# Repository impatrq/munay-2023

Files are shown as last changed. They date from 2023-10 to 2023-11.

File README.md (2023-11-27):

<div align="center">

# [Proyecto Munay - IMPA TRQ](https://www.instagram.com/proyecto_munay/)

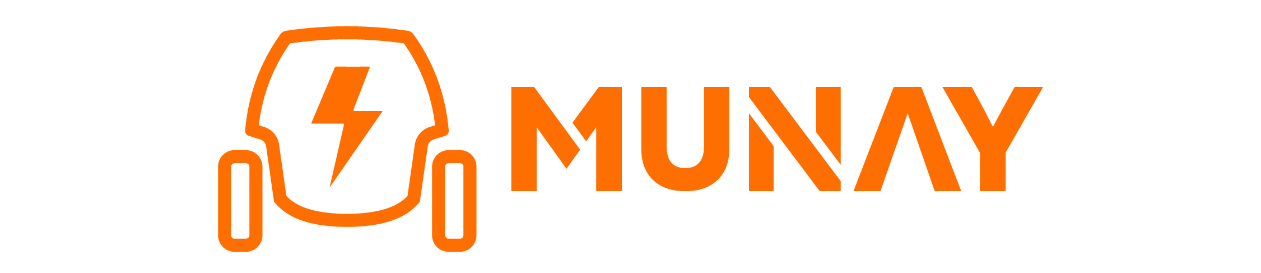
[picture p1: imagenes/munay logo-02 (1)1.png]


&nbsp;

| Página web | Email | Instagram |
|---|---|---|
|[Munay Web](https://proyectomunay.github.io/)|munay.impatrq@gmail.com|[@proyecto_munay](https://www.instagram.com/proyecto_munay/)|

&nbsp;

</div>

## ¿Qué es Munay?
Es un vehículo eléctrico diseñado específicamente para recorrer las pistas de las plazas aeroportuarias y llevar a cabo tareas como controlar la presencia de aves, señalero en pista y supervisar su estado general. Con este proyecto, buscamos acercar las últimas tecnologías al ámbito aeroportuario para modernizar sus procesos de control, supervisión y seguridad.

## ¿De dónde surgió la idea?
El proyecto Munay surgió a partir de una visita al aeropuerto Jorge Newbery (aeroparque), en la que se observó las diferentes modalidades de trabajo utilizadas y una de éstas fue la recorrida de pista. Se identificó que esta tarea conlleva mucho tiempo y recursos, y se consideró que era necesario buscar una solución innovadora para mejorar la eficiencia y la sostenibilidad en la industria aeroportuaria. Esto contribuiría a reducir los costos de operación y mantenimiento que se necesitan para un vehículo a combustión interna, que son los que se usan actualmente en este ámbito.

## Nuestra solución
Munay se destaca como un sistema de supervisión simplificado y altamente eficiente para la detección de FOD. Un vehículo eléctrico especialmente adaptado con cuatro cámaras estratégicamente ubicadas. Estas cámaras no solo proporcionan una vista precisa de la superficie terrestre, sino que, gracias a algoritmos de inteligencia artificial, también pueden detectar FOD tanto en tierra como en el cielo. Desarrollaremos un software personalizado que es esencial para esta solución. Cuando se conecta a Munay, ofrece una interfaz de usuario intuitiva que muestra las imágenes en tiempo real de las cuatro cámaras. La simplicidad es clave, los operadores solo necesitan traer su propia computadora de trabajo y conectarla al vehículo a través de USB en el soporte personalizado del auto.

## ¿Quiénes somos?

Somos un grupo de alumnos de E.E.S.T. N°7 "Taller Regional Quilmes" (IMPA).

### Basile, Ignacio Javier
* 📷 Instagram: basilee05

* 📧 ignaciojavierbasile@gmail.com

* LinkedIn: https://www.linkedin.com/in/demian-heis/

### Echezuria Gonzalez, Jorge Luis
* 📷 Instagram: jorgeechezuria_

* 📧 jlechezuria@gmail.com

* LinkedIn: https://www.linkedin.com/in/jorge-echezuria-60962a245/

### Heis, Demian Hernán
* 📷 Instagram: demian.h_

* 📧 demiheis@gmail.com

* LinkedIn: https://www.linkedin.com/in/demian-heis/

### Minaya Palomino, Jesús Eduardo
* 📷 Instagram: jesusminaya_

* 📧 jesusminayapalomino@gmail.com

* LinkedIn: http://www.linkedin.com/in/jesus-minaya-53a314292

### Ordoñez, Lucero Soledad Rubi
* 📷 Instagram: lucero092_

* 📧 lucerosoledad56@gmail.com
  
* LinkedIn: https://www.linkedin.com/in/lucero-soledad-rub%C3%AD-ordo%C3%B1ez-6a7ab429b/

### Retamar, Faustina

* 📷 Instagram: faustinaar_

* 📧 retamarfaustinaa@gmail.com

* LinkedIn: https://www.linkedin.com/in/faustina-retamar-43ab861a6/

### Rios, Celeste Aylen
* 📷 Instagram: celestearios

* 📧 celesteaylenrios@gmail.com

* LinkedIn: https://www.linkedin.com/in/celestearios/

<div align="center">

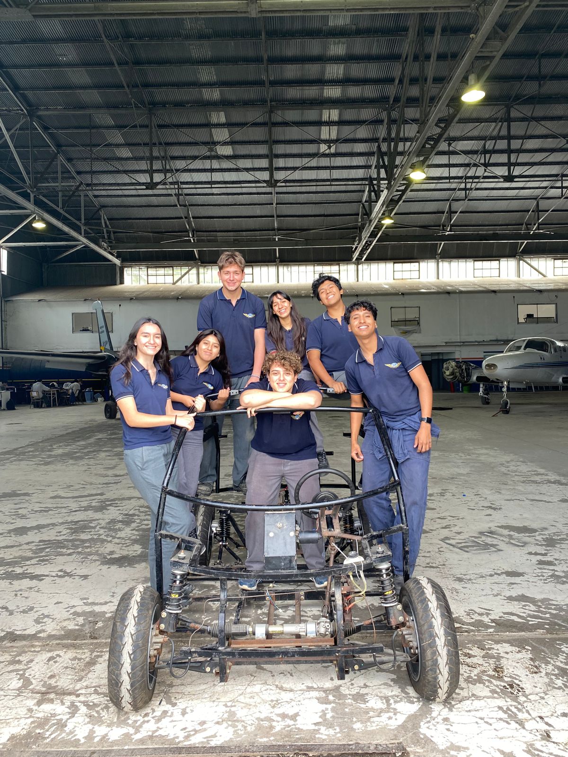
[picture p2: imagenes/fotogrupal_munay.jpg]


</div>

## ¿Cómo contactarnos?

* 📧 Email: munay.impatrq@gmail.com

* 🌐 Página Web: https://proyectomunay.github.io/

* 📷 Instagram: @proyecto_munay

* 🗞️ Linktr.ee: https://linktr.ee/proyecto_munay

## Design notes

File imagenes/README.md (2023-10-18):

<div align="center">

# [Proyecto Munay - IMPA TRQ](https://www.instagram.com/proyecto_munay/)



&nbsp;

| Página web | Email | Instagram |
|---|---|---|
|[Munay Web](https://www.google.com.ar/?hl=es)|munay.impatrq@gmail.com|[@proyecto_munay](https://www.instagram.com/proyecto_munay/)|

&nbsp;

</div>

## ¿Qué es Munay?

## ¿De dónde surgió la idea?

## ¿Cómo funciona?

## Tecnologías utilizadas

### Aplicación móvil

- Ionic con React
- Typescript
- Bootstrap

### Interfaz gráfica

- Electron
- React
- Typescript
- Bootstrap

### Esquemáticos

- KiCad

### Página web

- Next.js
- Typescript
- TailwindCSS
- Bootstrap

### Base de datos

- Firebase Realtime Database

### Microcontrolador

- uPython

### Planos

- AutoCAD

## ¿Quiénes somos?

Somos un grupo de alumnos de E.E.S.T. N°7 "Taller Regional Quilmes" (IMPA).

### Basile, Ignacio Javier
--> 📷 Instagram: basilee05

--> 📧 ignaciojavierbasile@gmail.com

### Echezuria Gonzalez, Jorge Luis
--> 📷 Instagram: jorgeechezuria_

--> 📧 jlechezuria@gmail.com

### Heis, Demian Hernán
--> 📷 Instagram: demian.h_

--> 📧 @gmail.com

### Minaya, Jesús Eduardo
--> 📷 Instagram: jesusminaya_

--> 📧 @gmail.com

### Ordoñez, Lucero Soledad Rubi
--> 📷 Instagram: lucero092_

--> 📧 @gnmail.com

### Retamar, Faustina
--> 📷 Instagram: faustinaar_

--> 📧 @gmail.com

### Rios, Celeste Aylen
--> 📷 Instagram: celestearios

--> 📧 @gmail.com

<div align="center">



</div>

## ¿Cómo contactarnos?

* 📧 Email: munay.impatrq@gmail.com

* 🌐 Página Web: xx

* 📷 Instagram: @proyecto_munay

* 🗞️ Linktr.ee: https://linktr.ee/proyecto_munay

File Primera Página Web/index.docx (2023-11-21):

Munay - IMPA TRQ

- Home
- About
- Contact

Auto eléctrico

para una supervisión eficiente

¿Qué es y cuál es el objetivo?

Munay es un vehículo eléctrico que será utilizado para la recorrida de pista en las plazas aeroportuarias, cumpliendo tareas como el control de aves, señalero de pista, y haciendo una supervisión general del estado de la misma.

Con MUNAY acercaremos las nuevas tecnologías en el ámbito aeroportuario. Modernizando sus procesos de control, supervisión y seguridad.

En base a las ventajas de utilizar MUNAY como vehículo de control destaca...

La referida a la reducción de emisiones de gases de efecto invernadero y de otros contaminantes en el aire.

Los costos de operación son más bajos en comparación con los vehículos de combustión interna, los que generalmente son utilizados en este ámbito, así resultaría esto en un ahorro significativo para el aeropuerto a largo plazo.

Visita a aeroparque

En febrero de 2023 hicimos una visita al aeropuerto "Jorge Newbery" (aeroparque) e investigando un poco nos dimos cuenta que es una zona con mucha energía solar sin aprovecharse, debido a ello crearemos un sistema de carga solar para el vehículo y así reducir el costo y mantenimiento que necesita un auto a combustión interna (que son los utilizados en la actualidad).

Instagram: @proyecto_munay | Linktree: @proyecto_munay | Mail: munay.impatrq@gmail.com

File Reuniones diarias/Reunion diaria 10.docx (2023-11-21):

# Miembros:

- BASILE, Ignacio Javier
- ECHEZURIA GONZALEZ, Jorge Luis
- HEIS, Demian Hernan
- MINAYA PALOMINO, Jesús Eduardo
- ORDOÑEZ, Lucero Soledad Rubí
- RETAMAR, Faustina
- RIOS, Celeste Aylen

# Trabajo actual

Planificación de las actividades a trabajar con OM001 ; OM003 ; HU001 ; HU002 ; HU009

# Expectativa del día

1. Terminaciones de la GUI
a. HU002G4 (https://trello.com/c/hfgtvepv) -> Minaya Jesús

2. Soldar

a. OM001B3 (https://trello.com/c/YOWDd1Iy) -> Echezuria Jorge; Heis Demian

3. Definir la frecuencia del envío

a. HU001E2 (https://trello.com/c/4T0kK5Ga) -> Retamar Faustina

4. Conexión y Prueba del Circuito

a. OM003C2 (https://trello.com/c/Cb8Cf4MF) -> Basile Ignacio, Ordoñez Lucero

5. Interfaz gráfica

a. HU009C3 (https://trello.com/c/GDZwJFuE) -> Ordoñez Lucero, Rios Celeste

# Observación:

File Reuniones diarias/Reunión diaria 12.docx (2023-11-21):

# Miembros:

- BASILE, Ignacio Javier
- ECHEZURIA GONZALEZ, Jorge Luis
- HEIS, Demian Hernan
- MINAYA PALOMINO, Jesús Eduardo
- ORDOÑEZ, Lucero Soledad Rubí
- RETAMAR, Faustina
- RIOS, Celeste Aylen

# Trabajo actual

Planificación de las actividades a trabajar con OM004 ; HU002 ; OM003 ; HU018

# Expectativa del día

1. Crear el programa que entrene la IA
a. HU002C2 (https://trello.com/c/GfMNkTXK) -> Minaya Jesús

2. Diseño de piezas

a. OM004A1 (https://trello.com/c/0t3vdllK) -> Basile Ignacio; Heis Demian

3. Carpeta de campo

a. HU018A (https://trello.com/c/BrOlQ3Z9) -> Echezuria Jorge ; Minaya Jesús

4. Calcular costos de pantalla y Terminaciones de la GUI

a. HU002F2 (https://trello.com/c/AScfl0pu) y HU002G4 (https://trello.com/c/hfgtvepv) -> Retamar Faustina; Rios Celeste

5. Terminaciones de la GUI

a. HU002G4 (https://trello.com/c/hfgtvepv) -> Retamar Faustina ; Rios Celeste

6. Reconexión de la palanca de cambios

a. OM003B6 (https://trello.com/c/YXXsG0NT) -> Echezuria Jorge; Ordoñez Lucero

# Observación:

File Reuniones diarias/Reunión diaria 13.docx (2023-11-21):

# Miembros:

- BASILE, Ignacio Javier
- ECHEZURIA GONZALEZ, Jorge Luis
- HEIS, Demian Hernan
- MINAYA PALOMINO, Jesús Eduardo
- ORDOÑEZ, Lucero Soledad Rubí
- RETAMAR, Faustina
- RIOS, Celeste Aylen

# Trabajo actual

Planificación de las actividades a trabajar con HU002 ; HU009 ; OM003; OM004; OM001

# Expectativa del día

1. Calcular costos de pantalla
a. HU002F2 (https://trello.com/c/AScfl0pu) -> Retamar Faustina

2. Botonera de la interfaz gráfica

a. HU002G6 (https://trello.com/c/lPkaCEpE) -> Retamar Faustina

3. Investigación de la comunicación-interfaz

a. HU009B2 (https://trello.com/c/D3MURqXc) -> Ordoñez Lucero; Rios Celeste

4. Diseño de piezas

a. OM004A1 (https://trello.com/c/0t3vdllK) -> Basile Ignacio ; Heis Demian

5. Switch (llave)

a. OM003B6 (https://trello.com/c/q51soJW4) -> Ordoñez Lucero

6. Pintar y lijar estructura

a. OM003D1 (https://trello.com/c/RGVBPgmT) -> Echezuria Jorge; Rios Celeste

7. Crear el programa que entrene la IA

a. HU002C2 (https://trello.com/c/GfMNkTXK) -> Minaya Jesús

8. Corrección de torsión en la parrilla

a. OM001C (https://trello.com/c/eUWS69it) -> Heis Demian

# Observación:

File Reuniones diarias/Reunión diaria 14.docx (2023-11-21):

# Miembros:

- BASILE, Ignacio Javier
- ECHEZURIA GONZALEZ, Jorge Luis
- HEIS, Demian Hernan
- MINAYA PALOMINO, Jesús Eduardo
- ORDOÑEZ, Lucero Soledad Rubí
- RETAMAR, Faustina
- RIOS, Celeste Aylen

# Trabajo actual

Planificación de las actividades a trabajar con HU002 ; HU009 ; OM004; OM001

# Expectativa del día

1. Botonera de la interfaz gráfica

a. HU002G6 (https://trello.com/c/lPkaCEpE) -> Retamar Faustina

2. Investigación de la comunicación-interfaz

a. HU009B2 (https://trello.com/c/D3MURqXc) -> Ordoñez Lucero; Rios Celeste

3. Diseño de piezas

a. OM004A1 (https://trello.com/c/0t3vdllK) -> Basile Ignacio

4. Inferencia utilizando Opencv

a. HU002D2 (https://trello.com/c/JhfQWf2p) -> Minaya Jesús

5. Corrección de torsión en la parrilla

a. OM001C (https://trello.com/c/eUWS69it) -> Echezuria Jorge ; Heis Demian

# Observación:

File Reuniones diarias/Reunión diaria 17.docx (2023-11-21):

# Miembros:

- BASILE, Ignacio Javier
- ECHEZURIA GONZALEZ, Jorge Luis
- HEIS, Demian Hernan
- MINAYA PALOMINO, Jesús Eduardo
- ORDOÑEZ, Lucero Soledad Rubí
- RETAMAR, Faustina
- RIOS, Celeste Aylen

# Trabajo actual

Planificación de las actividades a trabajar con HU009; HU002; OM003; OM004

# Expectativa del día

1. Transmisión de datos

a. HU009B4 (https://trello.com/c/2LAP4XD2) -> Rios Celeste; Echezuria Jorge

2. Pruebas de la botoneras en la interfaz

a. HU002G7 (https://trello.com/c/7uwNMmGb) -> Retamar Faustina; Minaya Jesús

3. Conexión de alimentación tablet/monitor

a. OM003B6 (https://trello.com/c/DJl1E43K) -> Ordoñez Lucero

4. ]Instalación

a. OM004B3 (https://trello.com/c/c1TSl2E6) -> Basile Ignacio; Heis Demian

# Observación:

- Retamar Faustina (llegó tarde)
- Heis Demian (llegó tarde)

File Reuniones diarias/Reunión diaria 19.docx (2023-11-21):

# Miembros:

- BASILE, Ignacio Javier
- ECHEZURIA GONZALEZ, Jorge Luis
- HEIS, Demian Hernan
- MINAYA PALOMINO, Jesús Eduardo
- ORDOÑEZ, Lucero Soledad Rubí
- RETAMAR, Faustina
- RIOS, Celeste Aylen

# Trabajo actual

Planificación de las actividades a trabajar con HU002; HU009; OM004

# Expectativa del día

1. Transmisión de los datos

a. HU009B4 (https://trello.com/c/2LAP4XD2) -> Echezuria Jorge ; Rios Celeste

2. Fabricación de piezas

a. OM004A2 (https://trello.com/c/7y6zeGLg) -> Basile Ignacio ; Heis Demian

3. Pruebas de las botoneras en la interfaz

a. HU002G7 (https://trello.com/c/7uwNMmGb) -> Minaya Jesús

4. Diseñar y probar prompt para las alertas

a. HU002E4 (https://trello.com/c/ufm9qXok) -> Retamar Faustina

Observación:

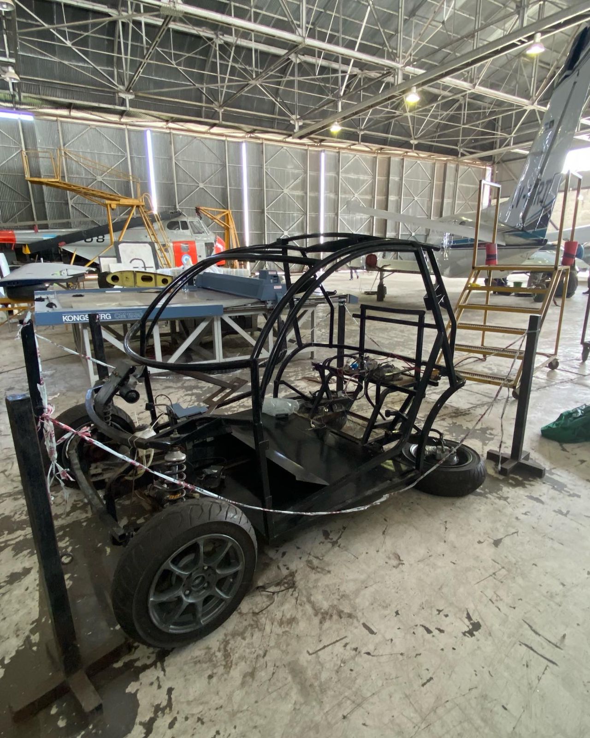
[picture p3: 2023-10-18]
Munay Web/images/gallery-images/gallery-image-7.jpg

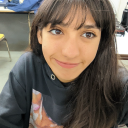
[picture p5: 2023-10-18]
Munay Web/images/user-images/rios.png

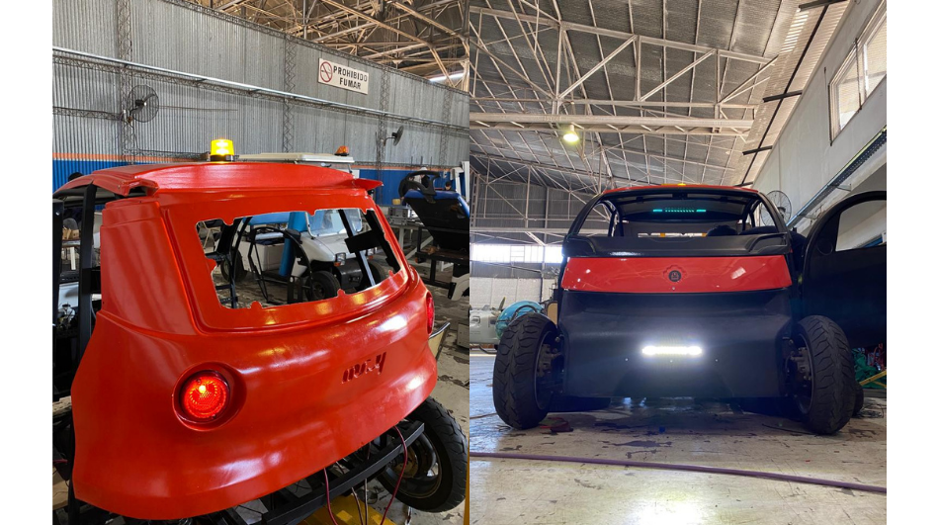
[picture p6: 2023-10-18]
Munay Web/images/gallery-images/gallery-image-16.png

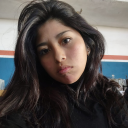
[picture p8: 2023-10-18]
Munay Web/images/user-images/ordoñez.png

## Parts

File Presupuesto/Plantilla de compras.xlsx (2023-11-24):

Adquirido | Cantidad | Componente | Link de referencia | Mejor precio | Por cantidad | Compra? | Proveedor | Prestado? | Escuela? | Devolver a:
FALSE | 1 | Ejemplo Sensor Presion Diferencial Mpx5100dp | CLICK (https://articulo.mercadolibre.com.ar/MLA-923254064-sensor-presion-diferencial-mpx5100dp-_JM) | $0.00 | $0.00 | FALSE | Intor (https://www.intor.com.ar/) | FALSE | FALSE
TRUE | 2 | Baterías | CLICK | $4000.00 | $8000.00 | FALSE | Aerocommander | TRUE | TRUE | Aerocommander
TRUE | 2 | Cable Usb a RS232 | CLICK (https://articulo.mercadolibre.com.ar/MLA-611815713-cable-adaptador-usb-a-serial-rs232-xtatil-local-belgrano-_JM) | $7.44 | $14.88 | TRUE | xTATIL (https://www.xtatil.com.ar/) | FALSE | FALSE
TRUE | 1 | MAX232 | CLICK (https://articulo.mercadolibre.com.ar/MLA-739213410-max-232-max-232-max232-max232cpe-rs-232-ttl-transceiver-_JM) | $3.25 | $3.25 | TRUE | Cyberofice (https://www.cyberofice.com.ar/) | FALSE | FALSE
TRUE | 1 | Conector DB9 Hembra | CLICK (https://articulo.mercadolibre.com.ar/MLA-800022729-adaptador-usb-20-a-hembra-db9-serie-hembra-_JM) | $1.20 | $1.20 | TRUE | AndesPC (https://www.andespc.com/) | FALSE | FALSE
TRUE | 2 | Tablet de 5" 2 GB de RAM Android | CLICK | $0.00 | $0.00 | FALSE | ENACOM (https://www.enacom.gob.ar/) | TRUE | FALSE | ENACOM
TRUE | 2 | Faros Led 160x80 - 120W | CLICK (https://articulo.mercadolibre.com.ar/MLA-867482995-par-de-faros-barras-auxiliar-led-cree-120w-spotflood-a-vip-_JM) | $32.34 | $64.68 | TRUE | Encedido Oeste | FALSE | FALSE
TRUE | 1 | Microcontrolador BeagleBone Black | CLICK (https://articulo.mercadolibre.com.ar/MLA-748742044-beaglebone-black-4g-arm-cortex-a-8-1ghz-4gb-original-rev-c-_JM) | $130.56 | $130.56 | FALSE | Fabrizio Carlassara | TRUE | FALSE | Carlassara Fabrizio
TRUE | 3 | Webcam Usb Xiaomi Imilab | CLICK (https://articulo.mercadolibre.com.ar/MLA-902320072-webcam-camara-web-para-pc-full-hd-1080p-con-microfono-noga-e-_JM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) | $9.14 | $27.42 | FALSE | ELECTROPOINT (https://www.electropoint.com.ar/) | FALSE | FALSE
TRUE | 1 | Cámara Watec modelo wat-01u2 | CLICK | $0.00 | $0.00 | FALSE | Diego Palmieri | TRUE | FALSE | Palmieri Diego
TRUE | 1 | micro-HDMI a HDMI | CLICK (https://articulo.mercadolibre.com.ar/MLA-901428738-cable-premium-micro-hdmi-a-hdmi-1-metro-hd-1080p-3d-vention-_JM) | $10.63 | $10.63 | TRUE | REDNETCorp (https://rednetcorp.com.ar/) | FALSE | FALSE
TRUE | 3 | Cables 5m Rojo-5m Verde-5m Marrón | CLICK (https://articulo.mercadolibre.com.ar/MLA-741624441-cable-unipolar-15-mm-negro-nomalizado-x-100m-fonseca-e631-_JM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) | $0.22 | $3.37 | TRUE | Eléctrica 361 (https://www.e631.com.ar/) | FALSE | FALSE
TRUE | 1 | Adaptador USB a HDMI Dehuka | CLICK (https://www.mercadolibre.com.ar/adaptador-compatible-macbook-pro-adaptador-usb-a-hdmi-video-1080p-dehuka/p/MLA21079140) | $10.17 | $10.17 | TRUE | DEHUKA (https://www.dehuka.com/) | FALSE | FALSE
TRUE | 2 | Amortiguador Trasero Jorsa | CLICK (https://articulo.mercadolibre.com.ar/MLA-1116735145-amortiguadores-vastago-corto-tras-peugeot-106-91-jorsa-_JM) | $114.00 | $228.00 | FALSE | Jorsa (http://www.jorsa.com.ar/index.htm) | FALSE | TRUE
TRUE | 2 | Motores QS motors | CLICK (https://www.qsmotor.com/product/3000w-205-car-motor/) | $310.00 | $620.00 | FALSE | QS Motors (https://www.qsmotor.com/) | FALSE | TRUE
TRUE | 1 | Parilla Delantera genérica | CLICK (https://articulo.mercadolibre.com.ar/MLA-871916024-juego-2-parrillas-de-suspension-c-rotula-renault-clio-12-_JM) | $142.00 | $142.00 | FALSE | RODINAG (https://www.rodinag.com/) | FALSE | TRUE
TRUE | 1 | Amortiguador Delantero Jorsa | CLICK (https://articulo.mercadolibre.com.ar/MLA-1116735145-amortiguadores-vastago-corto-tras-peugeot-106-91-jorsa-_JM) | $114.00 | $114.00 | FALSE | Jorsa (http://www.jorsa.com.ar/index.htm) | FALSE | TRUE
TRUE | 1 | Estructura Angulo Cuadrado genérico 22m | CLICK | $52.00 | $52.00 | FALSE | - | FALSE | TRUE
TRUE | 2 | Controladores Kelly KLS6022H | CLICK (https://kellycontroller.com/shop/brushless/) | $65.00 | $130.00 | FALSE | Kelly (https://kellycontroller.com/) | FALSE | TRUE
TRUE | 1 | Modulo Gps Gy-neo6mv2 Con Antena Raspberry Pic | CLICK (https://articulo.mercadolibre.com.ar/MLA-681823978-modulo-gps-gy-neo6mv2-con-antena-raspberry-pic-avr-arduino-_JM) | $8.00 | $8.00 | TRUE | DUAITEK | FALSE | FALSE
TRUE | 1 | Raspberry pi 4 | CLICK (https://articulo.mercadolibre.com.ar/MLA-885844516-raspberry-pi-4-model-b-4gb-ram-usb-c-element-14-_JM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) | $110.00 | $110.00 | FALSE | Sergio Medina | TRUE | FALSE | Medina Sergio
FALSE | 1 | - | CLICK | $0.00 | $0.00 | FALSE |  | FALSE | FALSE
FALSE | 1 | - | CLICK | $0.00 | $0.00 | FALSE |  | FALSE | FALSE
FALSE | 1 | - | CLICK | $0.00 | $0.00 | FALSE |  | FALSE | FALSE
FALSE | 1 | - | CLICK | $0.00 | $0.00 | FALSE |  | FALSE | FALSE
FALSE | 1 | - | CLICK | $0.00 | $0.00 | FALSE |  | FALSE | FALSE
FALSE | 1 | - | CLICK | $0.00 | $0.00 | FALSE |  | FALSE | FALSE
FALSE | 1 | - | CLICK | $0.00 | $0.00 | FALSE |  | FALSE | FALSE
FALSE | 1 | - | CLICK | $0.00 | $0.00 | FALSE |  | FALSE | FALSE

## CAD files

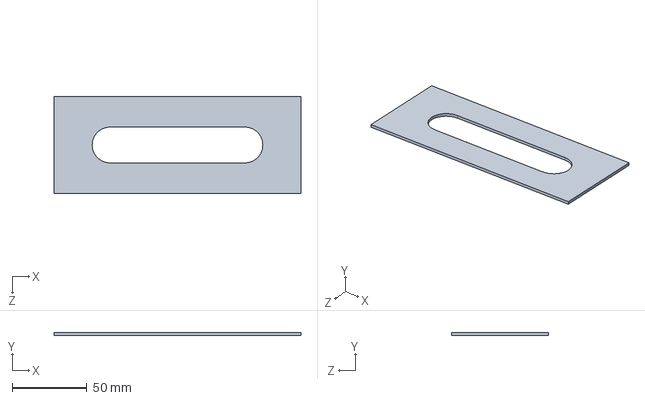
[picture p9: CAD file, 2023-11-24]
Diseños 3D/Archivos Solid Works/Base para Acelerador.SLDPRT
165.0 x 2.00 x 65.0 mm

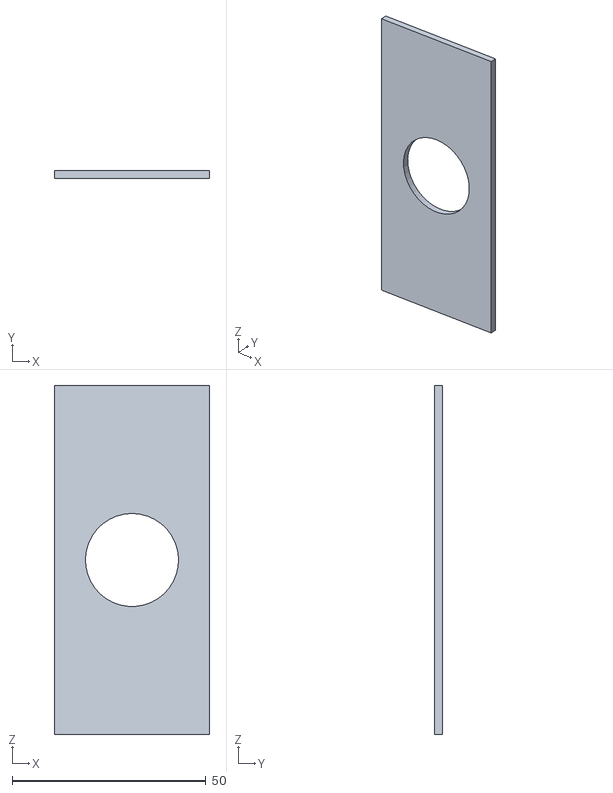
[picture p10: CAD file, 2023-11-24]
Diseños 3D/Archivos STL/Base para Acelerador.STL
40.0 x 2.00 x 90.0

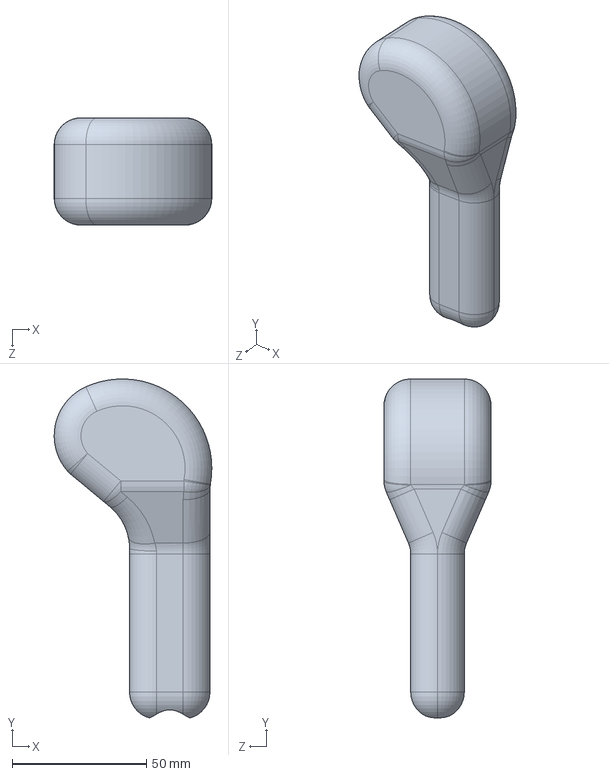
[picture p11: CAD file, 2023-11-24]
Diseños 3D/Archivos Solid Works/Palanca de Cambios.SLDPRT
58.8 x 126.4 x 40.0 mm

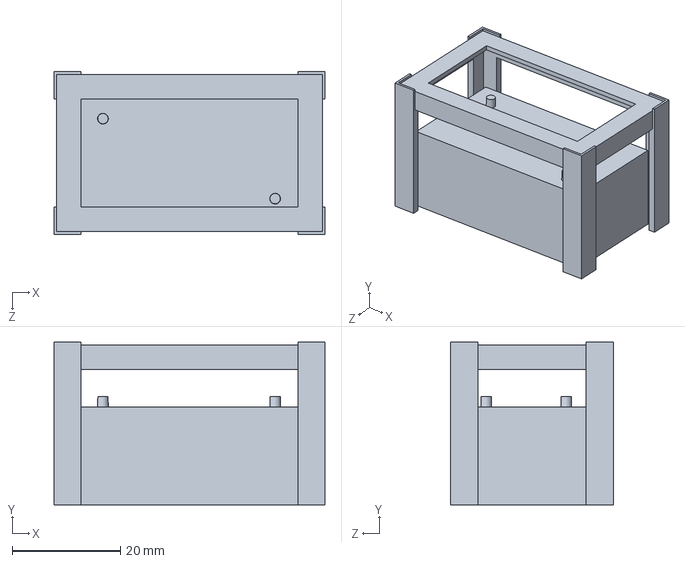
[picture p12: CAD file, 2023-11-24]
Diseños 3D/Archivos Solid Works/Estrructura Caja.SLDPRT
50.0 x 30.0 x 30.0 mm

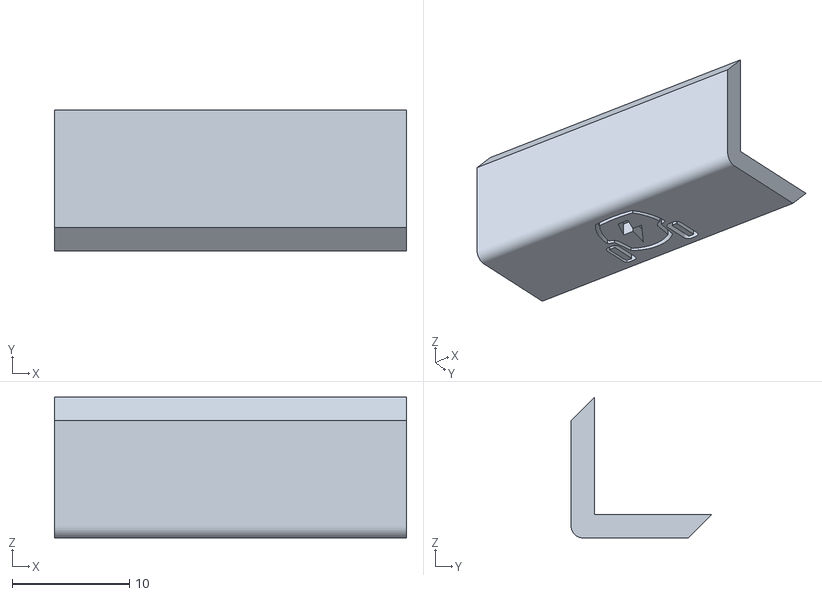
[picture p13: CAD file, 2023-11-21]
Diseños 3D/Archivos STL/Sold Arriba Embellesedor.STL
30.0 x 12.0 x 12.0

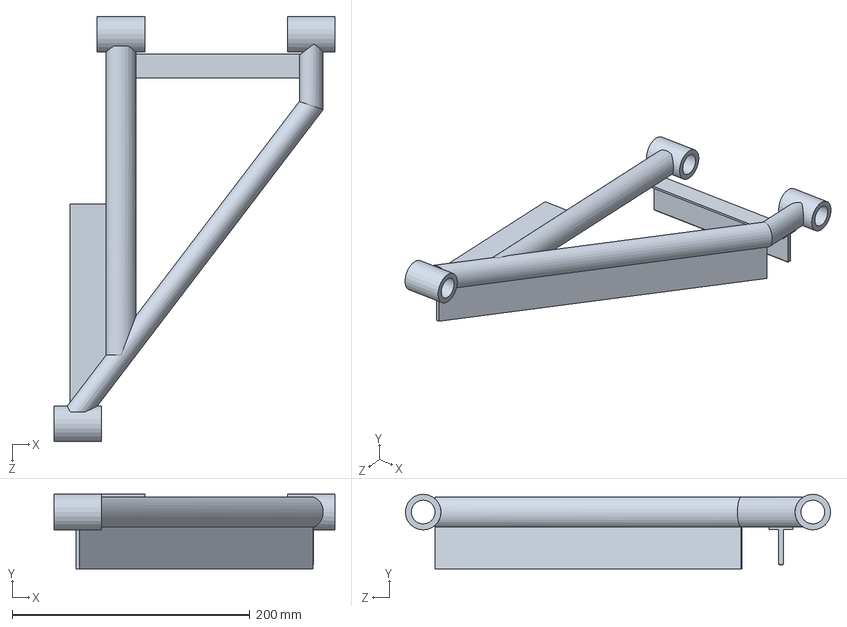
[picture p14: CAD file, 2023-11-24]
Diseños 3D/Archivos Solid Works/Parrilla Reforzada.SLDPRT
236.4 x 62.7 x 357.7 mm

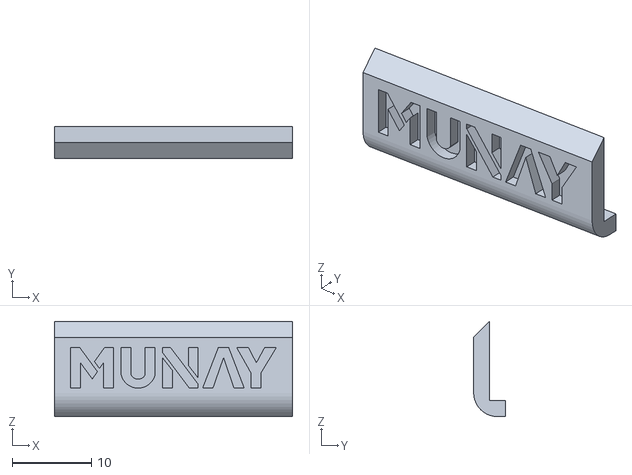
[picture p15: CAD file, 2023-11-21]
Diseños 3D/Archivos STL/Sold Abajo Embellesedor.STL
30.0 x 4.00 x 12.0

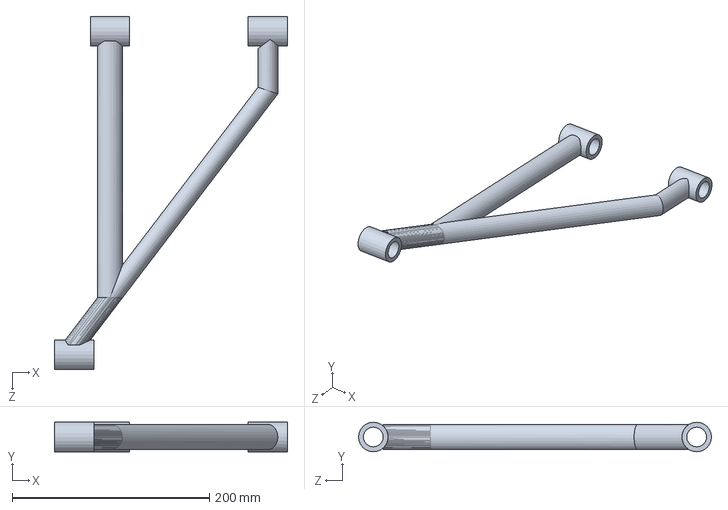
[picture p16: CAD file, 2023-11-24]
Diseños 3D/Archivos Solid Works/Parrilla Sin Refuerzo.SLDPRT
236.4 x 30.0 x 357.7 mm

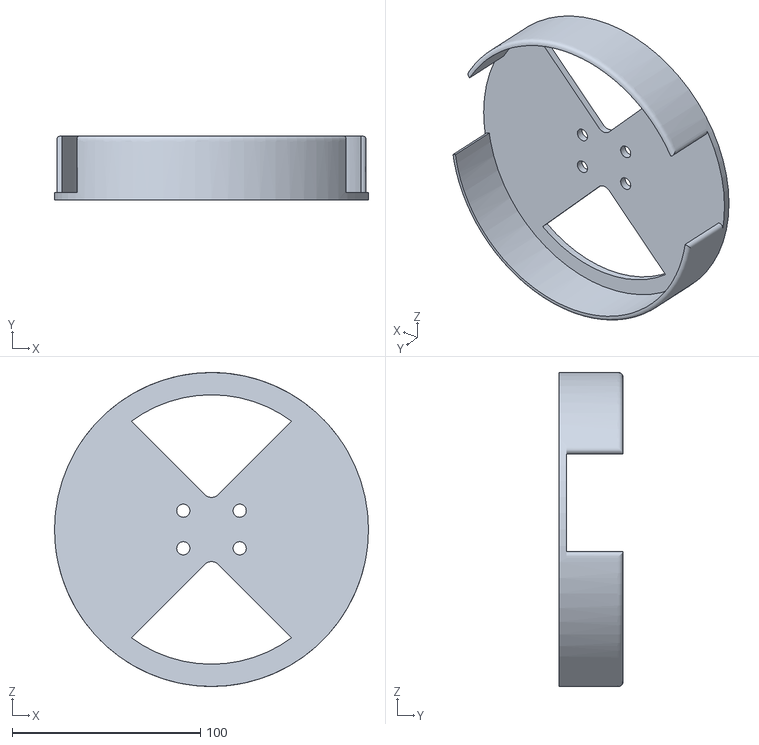
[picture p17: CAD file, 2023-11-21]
Diseños 3D/Archivos STL/Cubierta Volante.STL
167.0 x 34.0 x 167.0

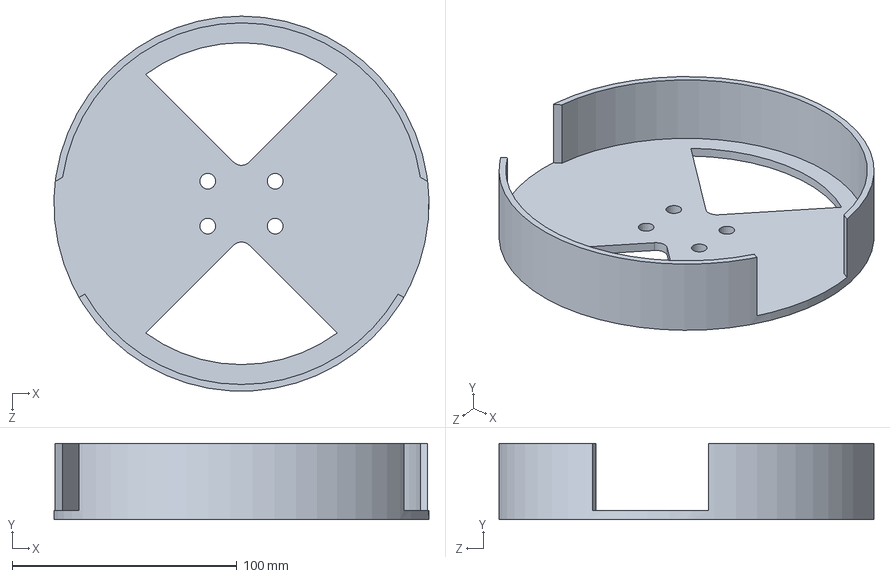
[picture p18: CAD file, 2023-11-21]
Diseños 3D/Archivos Solid Works/Soporte volante.SLDPRT
167.0 x 34.0 x 166.9 mm

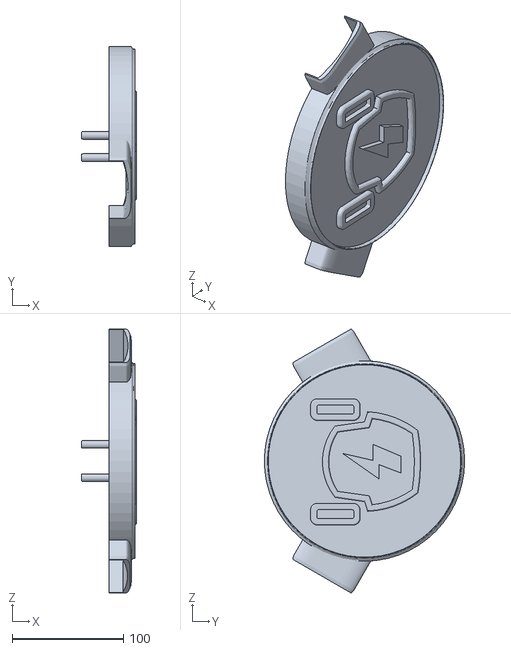
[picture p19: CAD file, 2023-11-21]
Diseños 3D/Archivos STL/Soporte de Volante.STL
49.0 x 180.0 x 237.2

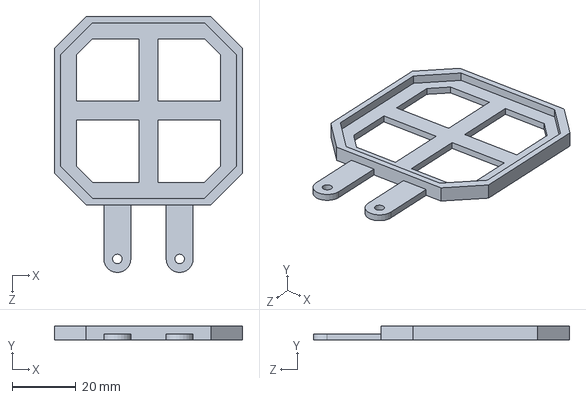
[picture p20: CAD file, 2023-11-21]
Diseños 3D/Archivos Solid Works/Soporte usb.SLDPRT
59.1 x 4.50 x 80.3 mm

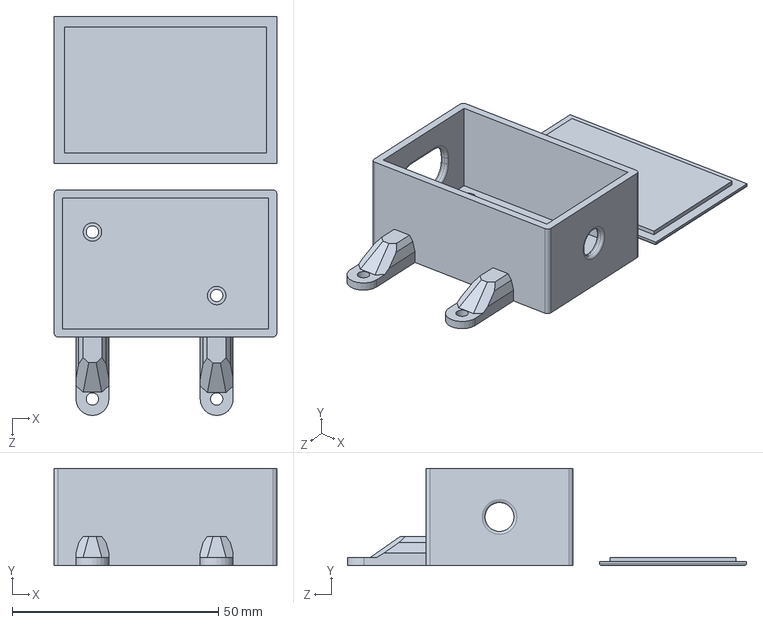
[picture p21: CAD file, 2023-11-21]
Diseños 3D/Archivos Solid Works/Reg Para Tablet Jack.SLDPRT
54.0 x 23.5 x 96.7 mm

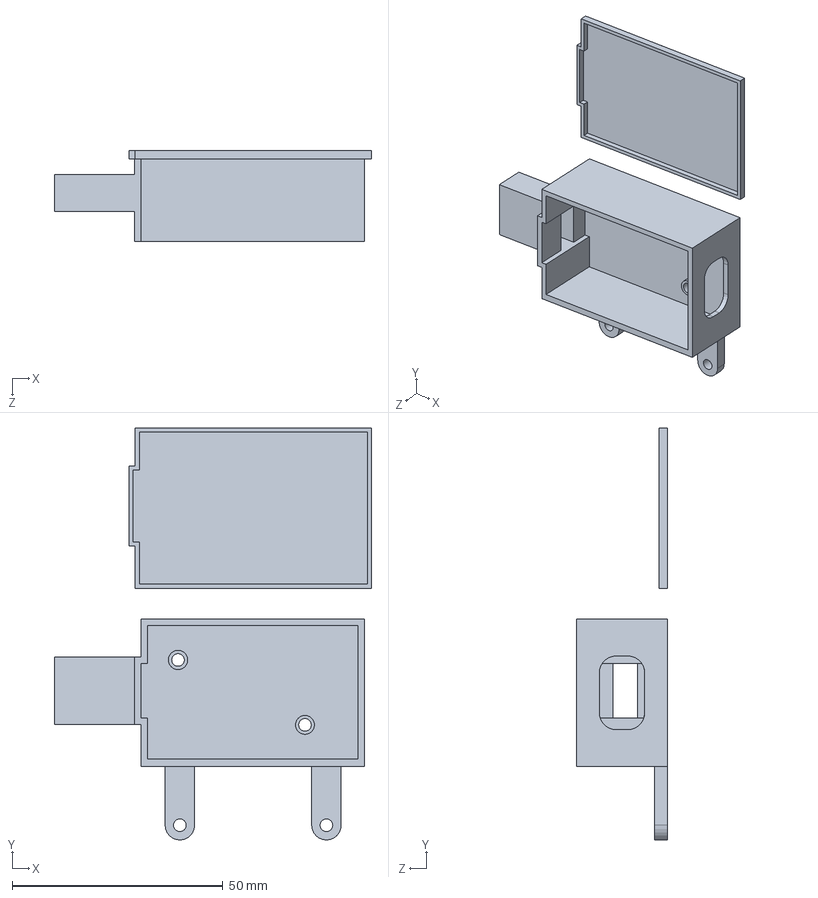
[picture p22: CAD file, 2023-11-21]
Diseños 3D/Archivos Solid Works/Reg Para Tablet A.SLDPRT
75.2 x 97.7 x 21.5 mm

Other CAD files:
Diseños 3D/Archivos STL/STL Palanca.STL
Diseños 3D/Archivos STL/Soporte usb.STL
Diseños 3D/Archivos STL/Reg Para Tablet Jack.STL
Diseños 3D/Archivos STL/Reg Para Tablet A.STL
Diseños 3D/Archivos STL/Camara Frente.STL
Diseños 3D/Archivos STL/Camara Piso.STL
Diseños 3D/Archivos STL/Covertor de rueda+Logo.STL
Diseños 3D/Archivos STL/Embellesedor Parte DER.STL
Diseños 3D/Archivos STL/Embellesedor Parte IZQ.STL
Diseños 3D/Archivos STL/Funda Tablet Bien 3.STL
Diseños 3D/Archivos STL/Logo Frente del auto.STL
Diseños 3D/Archivos Solid Works/Camara Frente.SLDPRT
Diseños 3D/Archivos Solid Works/Camara Piso.SLDPRT
Diseños 3D/Archivos Solid Works/Covertor de rueda+Logo.SLDPRT
Diseños 3D/Archivos Solid Works/Cubierta Volante.SLDPRT
Diseños 3D/Archivos Solid Works/Embellesedor Parte DER.SLDPRT
Diseños 3D/Archivos Solid Works/Embellesedor Parte IZQ.SLDPRT
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

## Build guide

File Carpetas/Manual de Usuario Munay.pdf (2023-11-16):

# MUNAY

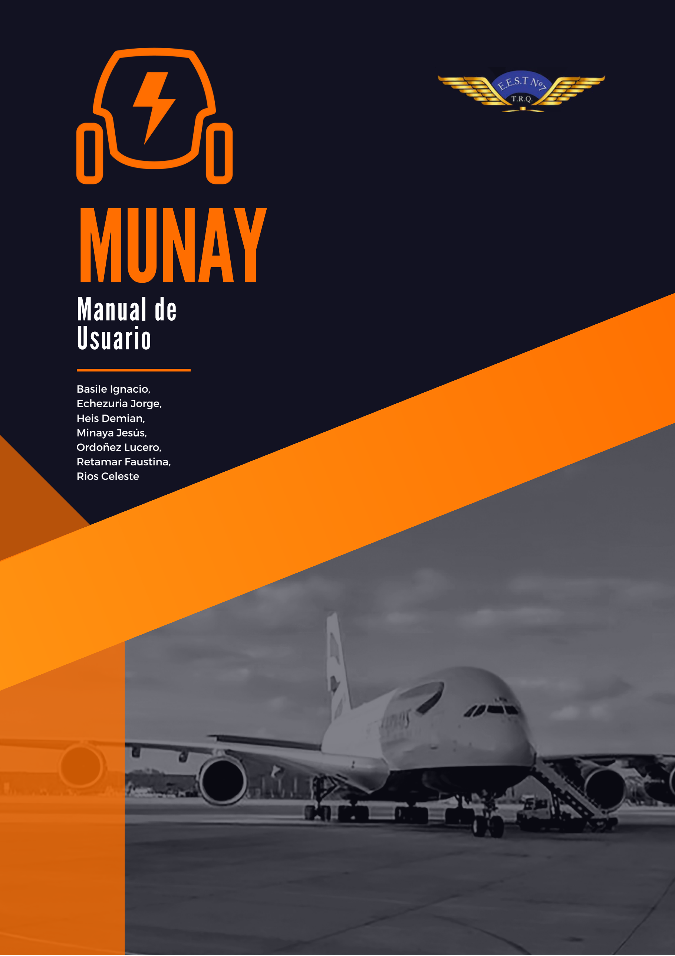
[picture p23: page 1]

# Manual de Usuario

Basile Ignacio, Echezuria Jorge, Heis Demian, Minaya Jesús, Ordoñez Lucero, Retamar Faustina, Rios Celeste

# ÍNDICE

1. Introducción | 3
2. Seguridad para conducir | 3
3. Baterías | 4
3.1 Baterías traseras | 4
3.1.1 Procedimiento de carga | 4
3.1.2 Precauciones, atenciones y advertencias | 6
4. Autonomía | 8
4.1 Recomendaciones para mantener su autonomía | 8
5. Sistemas de propulsión y electrónica | 8
5.1 Motores | 8
5.2 Controladores | 8
6. Componentes del sistema | 9
6.1 Cámaras | 9
6.2 Inteligencia Artificial | 10
6.3 Interfaz gráfica | 10
6.3.1 Pasos para iniciar la interfaz gráfica | 11
6.4 Visualización de imágenes en tiempo real | 12
6.5 Botones y configuración de la interfaz grafica | 13
6.6 Bot de Telegram | 16
6.6.1 Configuración del destinatario | 16
6.6.1.1 Obtener su ID de chat en Telegram | 17
6.7 Detectar FOD | 17
6.7.1 Procedimientos luego de detección de FOD | 17
7. Luces | 18

### 7.1 Ubicación de las luces 7.2 Precauciones

## Guía para el Personal de Mantenimientos de Aeropuertos

Antes de encender tu vehículo, asegúrate de que el conector de carga esté desconectado.
Antes de encender tu vehículo, asegúrate de que la perilla de cambio de marcha esté en posición de neutro (N).
Enciende tu vehículo y comprueba el dashboard, la interfaz gráfica, todas las luces de señalización, y las cámaras. Asegúrate de que las cámaras estén limpias y sin obstrucciones que puedan afectar la detección de FOD.
Para asegurarte de no obstruir los pedales, verificá que no haya obstáculos de en el área de los mismos.
Comprueba que el sistema de iluminación y la sirena funcione correctamente
Para garantizar que viajes de manera segura, revisa los asientos y cinturones de seguridad
Antes de conducir, asegúrate de abrochar apropiadamente el cinturon de seguridad, revisar el ángulo del retrovisor, y fijarte que las puertas estén completamente cerradas.
Comprueba el porcentaje de carga de la batería en el tablero de instrumentos.

# 1. INTRODUCCIÓN

En el mundo dinámico de la aviación, la seguridad es primordial. Enfrentando el desafío de los "restos de objetos extraños" (FOD), Munay redefine la vigilancia en las pistas aeroportuarias. Desde diminutas piezas metálicas hasta objetos más imponentes, asegurando que cada rincón del aeropuerto esté libre de obstáculos, garantizando así la seguridad y eficiencia en la operación aeroportuaria.

# 2. SEGURIDAD PARA CONDUCIR

¡Antes de operar el vehiculo asegurese de haber leído atentamente el manual de usuario!

Apague el vehículo antes de cargar las batería. Es necesario que el vehículo se encuentre apagado para mayor seguridad. Tanto para las dos baterias traseras verifique que las especificaciones de ambas se ajusten a Munay y que estén en buen estado, sin daños, fugas o signos de desgaste.
Para la conexiones de carga asegúrese que el cargador de las baterías esté en buenas condiciones

# 3. BATERIAS

Cómo cargar las baterías
Cargar las baterías de Munay es una tarea esencial para garantizar su funcionamiento seguro y confiable. A continuación, se proporciona una guía paso a paso que explica cómo cargar estas baterías, teniendo en cuenta que esto puede variar según el tipo de aeronave del que se haya extraído su batería.

Para ello, utiizaremos un cargador, en donde se va a enchufar en el lado izquierdo del vehículo, con una ficha de tipo industrial . Este estará conectado directamente a las baterías aeronáuticas.

## 3.1 Baterías traseras

Estas baterías son fundamentales para Munay, ya que, estas alimentan al Controlador Kelly que es una pieza clave para el arranque del vehículo.

### 3.1.1 Procedimiento de carga

Antes de comenzar el proceso de carga de las baterías aeronáuticas en Munay, asegúrate de seguir estos pasos de preparación:

Asegúrese que las conexiones del cable de carga estén firmes y seguras. Si no está bien ajustada, puede ocasionar una carga fantasma en las baterías, o deformarlas. Configure el equipo de carga de acuerdo a las especificaciones del fabricante y las necesidades de las baterías aeronáuticas:
Ajuste el voltaje y la corriente de carga según las especificaciones de las baterías. No exceda los límites recomendados.
Establezca el tiempo de carga de acuerdo a las necesidades de las baterías y su nivel de descarga.
Encienda el cargador de baterías de acuerdo con las instrucciones del fabricante.
Durante el proceso de carga, supervise continuamente el estado de las baterías y el equipo de carga para detectar cualquier anomalía. Recuerde evitar el aumento de temperatura en las baterías.
Cuando se haya completado el proceso de carga desconecte el cargador de baterías del cable de carga y apáguelo.

No excedas los límites de carga recomendados para evitar daños a las baterías y posibles riesgo.
No permitas que los cables de carga entren en contacto con objetos metálicos que puedan causar cortocircuitos.
Nunca intentes cargar baterías dañadas o con fugas. Sustitúyelas antes de la carga.
La carga de baterías del vehículo es una tarea crítica que debe realizarse con precaución y siguiendo las pautas del fabricante. Si no está seguro de cómo hacerlo, consulte a un profesional de mantenimiento de aeronaves calificado.

## 3.1.2 Precauciones, Atenciones y Advertencias

# 4. AUTONOMIA

Debe de tener en cuenta que su tiempo máximo de uso está estimado en una hora, en la que usted recorrerá un aproximadamente una distancia de 30Km. Además el vehículo consume 0,0216 kilovatios - hora por kilometro que recorre.

## 4.1 Recomendaciones para mantener su autonomía

Procure conducir a velocidades reducidas para proteccion de la autonomía. Evite aceleraciones y frenadas bruscas que provocarían aumentar el consumo de energía.

# 5. SISTEMA DE PROPULSION Y ELECTRONICA

## 5.1 Motores

El nombre del motor es QSWP 48V 2000W1 70612. El modelo de ambos motores es QS de ejes unicos, ideales para coches electricos. Su voltaje nominal es de 48v . La potencia nominal es de 2000 vatios, lo que significa que esta es la potencia máxima que el motor puede suministrar continuamente en condiciones normales.

## 5.2 Controladores

El vehículo cuenta con los controladores Kelly KLS6022H. Los controladores de motor programables Kelly brindan controles eficientes, suaves y silenciosos para motocicletas eléctricas, carritos de golf y go-karts, así como control de motores industriales.

Cámara Frontal: Ubicada en la parte delantera del vehículo.Detecta problemas en la pista, como desgaste o acumulación de objetos extraños (F.O.D.).
Cámaras Superiores (tres): Situadas en la parte superior del vehículo con un ángulo de separación de 120 grados. Amplían significativamente el campo de visión sin necesidad de salir del vehículo. Y detectan el movimiento de aves, lo que contribuye a prevenir riesgos para la seguridad aeroportuaria.

# 6. COMPONENTES DEL SISTEMA

Los componentes del sistema se refieren al conjunto de elementos que conforman la llamativa tecnología de Munay, y estos son las cámaras, la inteligencia artificial con su interfaz grafica, el dashboard, etc. A continuación se explican y detallan cada una de ellas para su correcta operacion.

## 6.1 Cámaras

Munay integra un conjunto de cámaras de alto rendimiento, cada una con funciones específicas.

1.

2. (https://e-vehicle.eu/KellyKLS-HUserManualV1.10.pdf)

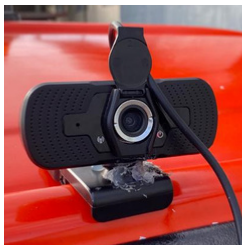
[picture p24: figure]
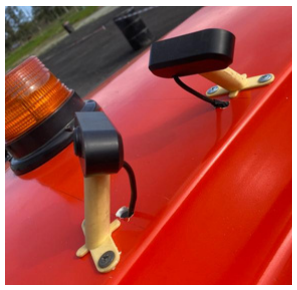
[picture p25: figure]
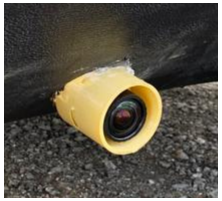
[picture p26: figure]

## 6.2 Inteligencia Artificial

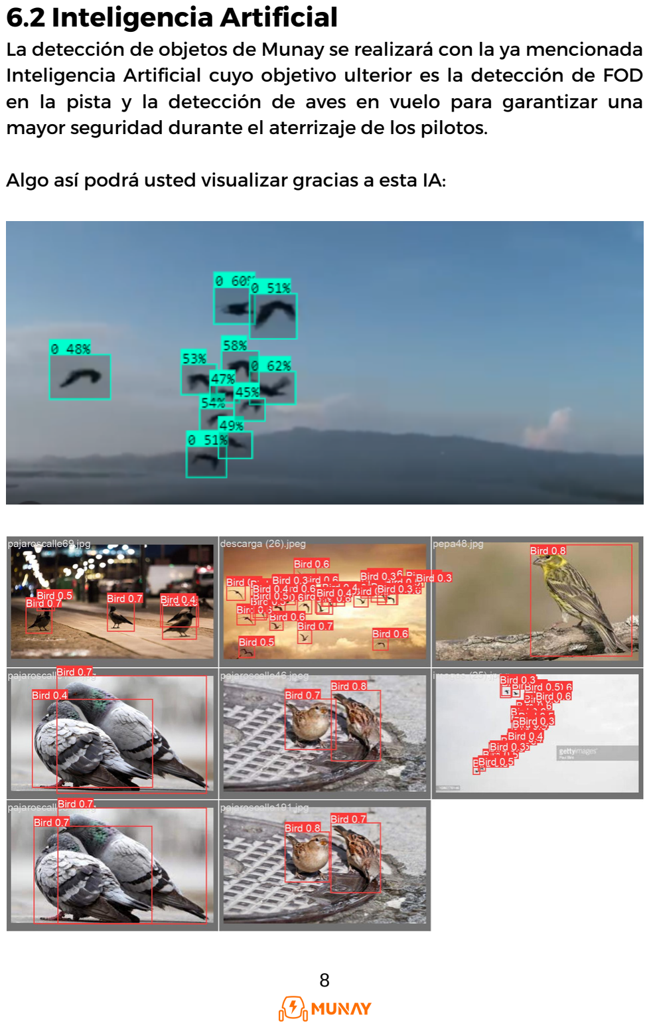
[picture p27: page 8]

La detección de objetos de Munay se realizará con la ya mencionada Inteligencia Artificial cuyo objetivo ulterior es la detección de FOD en la pista y la detección de aves en vuelo para garantizar una mayor seguridad durante el aterrizaje de los pilotos.

Algo así podrá usted visualizar gracias a esta IA: (https://e-vehicle.eu/KellyKLS-HUserManualV1.10.pdf)

El instalador de la interfaz gráfica se encuentra en la página web de Munay. Puede acceder a ella mediante el siguiente link o QR.

## 6.3 Interfaz Gráfica

Para utilizar la inteligencia artificial, se empleará una interfaz gráfica a través de la cual se podrá activar la IA. Esta interfaz estará disponible para su descarga desde la página oficial de Munay.

6.3.1 Pasos para descargar tu Interfaz gráfica (https://e-vehicle.eu/KellyKLS-HUserManualV1.10.pdf)

https://proyectomunay.github.io/

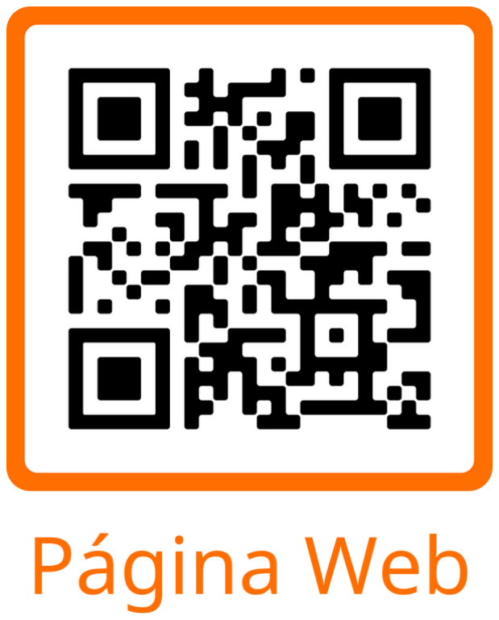
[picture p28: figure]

Seleccione el ícono que se presenta en la foto. Al apretarlo, se le descargará automáticamente el instalador de la interfaz gráfica y, ese mismo aparecerá en la barra de descargas de su plataforma.

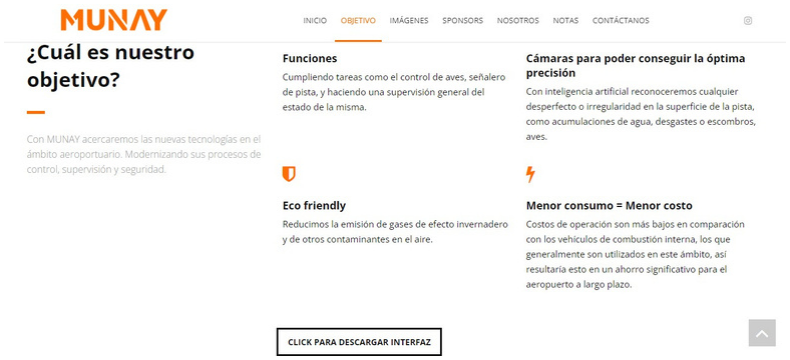
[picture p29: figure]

Luego que se haya cargado el instalador, se procede a ejecutar el programa. Le aparecerá una ventana de “selección de idioma que va a tener la interfaz gráfica”.

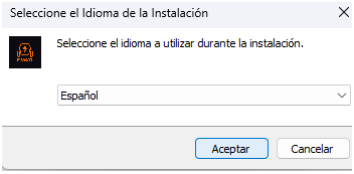
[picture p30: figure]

Después, le aparecerá una ventana de “escribir la contraseña del instalador del programa”. Esta contraseña se la daremos cuando compre nuestro servicio.

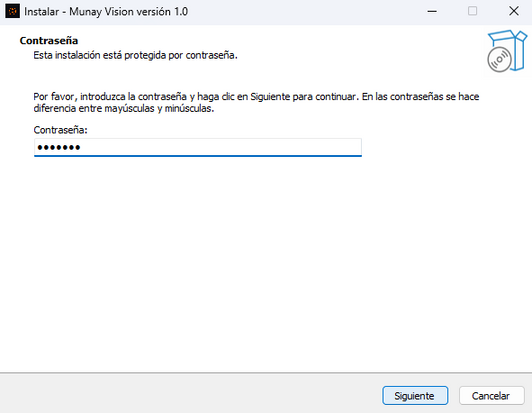
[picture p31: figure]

En la siguiente ventana, podrá seleccionar la ruta en donde va a estar el archivo en su computadora.

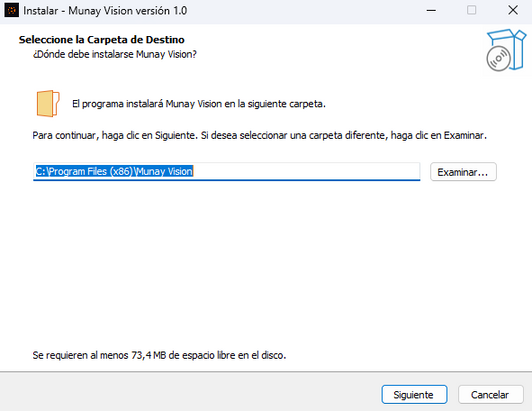
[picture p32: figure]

En la siguiente ventana, podrá seleccionar si el programa de la interfaz gráfica se pueda ejecutar en el Escritorio de la computadora mediante un Acceso Directo

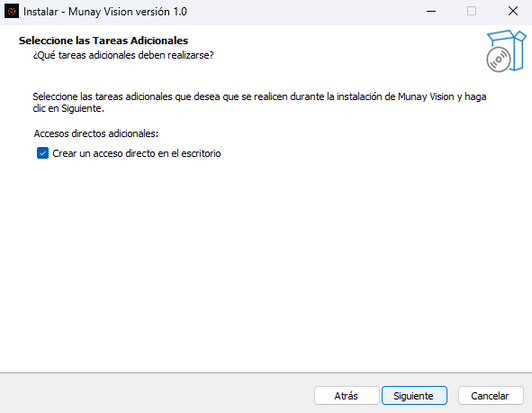
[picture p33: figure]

En la siguiente ventana, se podrá instalar el programa definitivamente en su computadora

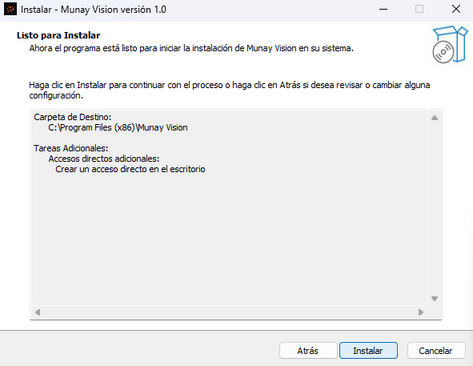
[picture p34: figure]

Una vez finalizada la descarga, ya podrá usar “Munay Vision”, la interfaz gráfica de Munay y, a su vez, la inteligencia artificial de detección de FOD.

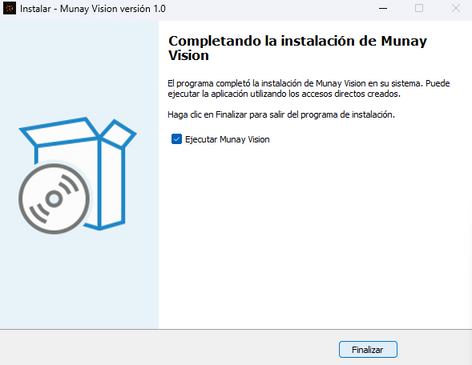
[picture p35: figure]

Primeramente aseguresé que la bateria delantera esté bien mantenida, alimentada y cargada.
Encienda su computadora y revise que ésta funcione correctamente al igual que todos sus puertos USB.
Luego verifique que el sistema operativo de su dispositivo esté instalado y actualizado a la última versión disponible.
Mantenga su dispositivo conectado a una red Wi-Fi o en caso de disponer de datos establecer una red para conectarse a ella. Ingrese los puertos USB que utilizará en la consola que lo solicita. Fijarse y anotar en donde conectó cada cámara en cada puerto de la computadora.
El dispositivo que se va a utilizar para poder visualizar la interfaz gráfica tiene que estar perfecta y solidamente acoplada al soporte que se encuentra en el tablero del vehículo para evitar accidentes.
Abrir el programa llamado “Munay Vision” ya instalado desde donde lo haya guardado.

### 6.3.1 Pasos para iniciar la interfaz gráfica

1.

2.

3.

4.

5.
6.

7.

8. (https://e-vehicle.eu/KellyKLS-HUserManualV1.10.pdf)

Acceso directo de la interfaz gráfica

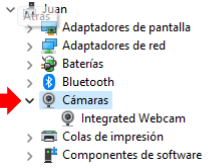
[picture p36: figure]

### 9. Al abrir el programa, le aparecerá una ventana que le permitirá al

usuario elegir cuántas cámaras va a usar. Dependiendo de en donde estén conectados los cables usb con los puertos de las cámaras cambiarán los números de las cámaras designadas. Pueden ser los números 0, 2, 3, y 4.

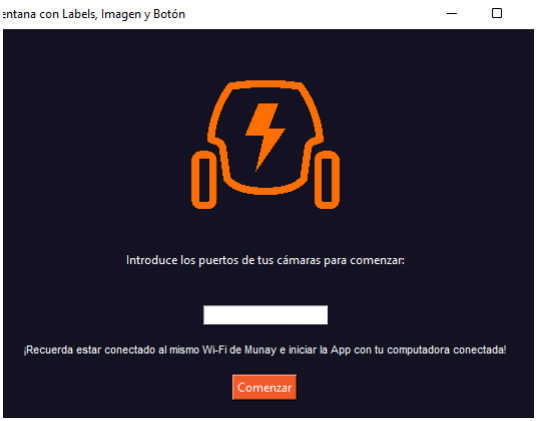
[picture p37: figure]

### 10. Ya esta todo listo para que pueda usar la interfaz gráfica, junto

con la inteligencia artificial.

### 8. Para fijarse los puertos de las cámaras, primero tienes que ir a

Administrador de dispositivos > Cámaras , y ahí aparecerán cuáles cámaras estan conectadas a tú computadora y en qué puesto de ella se encuentran.

## 6.4 Visualización de imágenes en tiempo real

En la interfaz de Munay, se mostrará las imágenes en tiempo real de las cuatro cámaras ubicadas en el vehículo. Usted visualizará esta interfaz en el tablero del vehículo, a la derecha de la tablet.

Una vista como esta deberia estar pudiendo observar:

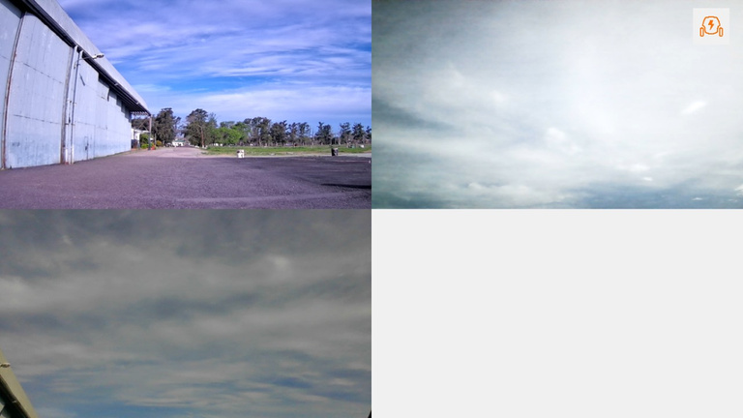
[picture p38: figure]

En tal caso de tener problemas o directamente no ver una de las cámaras revisar las conexiones de los puertos USB o considerar si ingresó correctamente el nombre su puerto al inicio de la configuracón del programa (https://e-vehicle.eu/KellyKLS-HUserManualV1.10.pdf)

## 6.5 Botones y configuración de la interfaz grafica

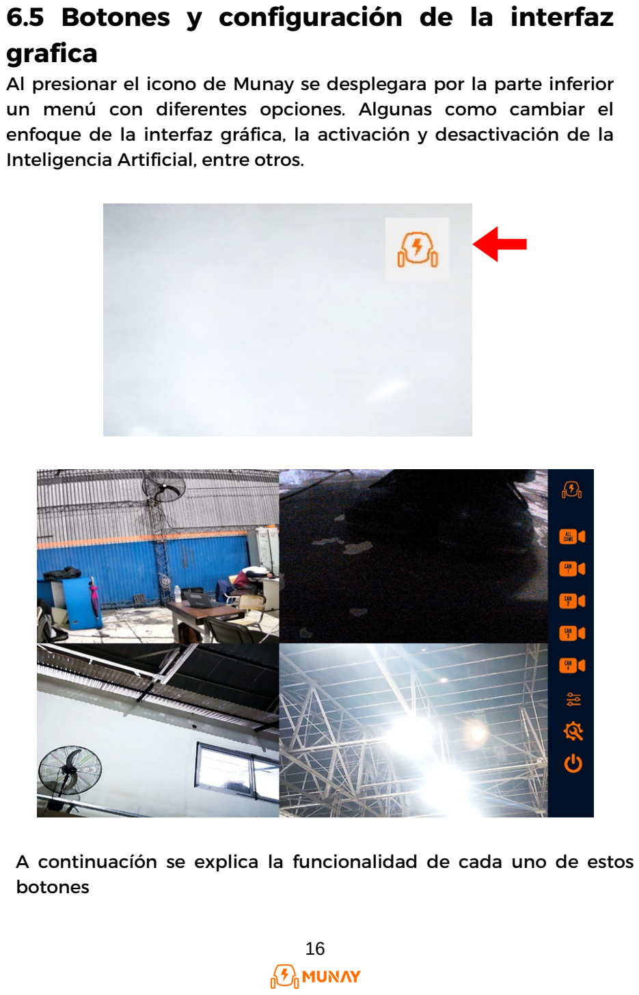
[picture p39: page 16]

Al presionar el icono de Munay se desplegara por la parte inferior un menú con diferentes opciones. Algunas como cambiar el enfoque de la interfaz gráfica, la activación y desactivación de la Inteligencia Artificial, entre otros.

A continuacíón se explica la funcionalidad de cada uno de estos botones (https://e-vehicle.eu/KellyKLS-HUserManualV1.10.pdf)

Si usted oprime este botón, podrá ver lo que observa la cámara superior delantera

Si usted oprime este botón, podrá ver lo que observa la cámara inferior delantera

Si usted oprime este botón, podrá ver lo que observa la cámara superior izquierda trasera

Si usted oprime este botón, podrá ver lo que observa la cámara superior derecha trasera

Si usted oprime este botón, podrá ver lo que observan todas las cámaras simultáneamente

Si usted oprime este botón, podrá elegir cambiar de filtros para las camaras delanteras o superiores,

Si usted oprime este botón, se apagará la interfaz. Eso incluye el sistema de detección de FOD y las cámaras

Activar/desactivar el sistema de detección de FOD
Configurar el Wi-Fi
Configurar Mail destino
Configurar Telegram

Si usted oprime este botón, podrá:

Acceda a la sección de configuración, como se explicó anteriormente, a través del botón "Configuración" en la aplicación Munay.
Dentro de la sección de configuración, busque la opción "Configuración de CHAT ID de Telegram" y selecciónela.

## 6.6 Bot de telegram

Este bot actúa como un canal de comunicación clave que permite la transferencia de información entre Munay y el supervisor en caso de encontrar un objeto FOD.

### 6.6.1 Configuración del destinatario

Para configurar el destinatario de las alertas que el usuario de Munay envía al supervisor, siga los siguientes pasos:
1.
2. (https://e-vehicle.eu/KellyKLS-HUserManualV1.10.pdf)

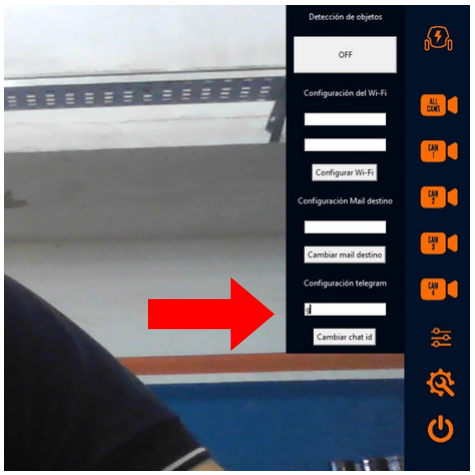
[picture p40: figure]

En la aplicación de Telegram abra el chat con su supervisor.
En la barra de direcciones de su navegador web, observe la URL. Debería tener una estructura similar a: https://web.telegram.org/k/#XXXXXXXXX. (https://web.telegram.org/k/#-XXXXXXXXX)

### 6.6.1.1 Obtener su ID de chat en Telegram

1.
2.

### 3. El ID que necesita para configurar el destinatario de sus datos se

encuentra después del símbolo "#" o despues del “@”. Consiste en una serie de números o es el propio usuario de la persona. Por ejemplo, si la URL es: https://web.telegram.org/k/#123456789.
El ID a utilizar sería -123456789.

### 4. Copie este ID y péguelo en el campo correspondiente en la

sección "Configuración de CHAT ID de Telegram" en la interfaz gráfica de Munay.

Si elige “Enviar alerta” se generará un mensaje de alerta que incluirá una imágen y un enlace de Google Maps con la ubicación exacta en dónde se detectó el objeto. Este mensaje se enviará al chat especificado a través de nuestro bot de Telegram.
Si selecciona “No es un FOD o Ave” ésta información se enviará a los algoritmos de la inteligencia artificial para mejorar su capacidad de detección en futuras ocasiones.

## 6.7 Detectar FOD

El sistema que utiliza Munay utiliza algoritmos de inteligencia artificial para detectar objetos extraños en tierra y aire. Los objetos extraños se resaltarán en la pantalla en caso de detección.

### 6.7.1 Procedimientos luego de detección de FOD

Cuando la Inteligencia Artificial detecte un objeto FOD, en la interfaz gráfica usted visualizará tres opciones en forma de ventanas emergentes, las cuales contendrán una imagen del objeto detectado.

## 7. Luces

A un costado inferior derecho se encuentrn unos switches. Las luces se encienden con la fila inferior. A continuación se le mostrará una imágen con las posiciones de los botones y el uso de cada uno de los mismos

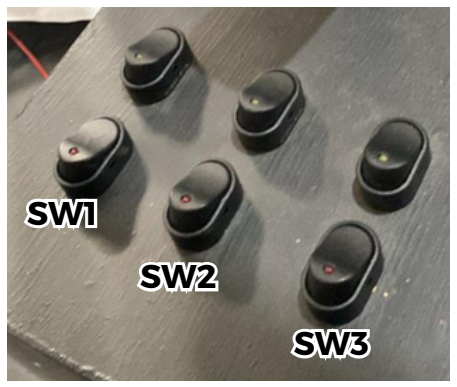
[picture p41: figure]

SW1: Con este botón usted encenderá el faro LED delantero. Este se utiliza para que la Inteligencia Artificial pueda seguir trabajando en plena oscuridad.
SW2: Con este botón usted encenderá una sirena lumínica. Este se utiliza para que los demás usuarios puedan reconocer a Munay a lo lejos.
SW3: Con este botón usted encenderá las luces traseras. Este se utiliza para alertar a las personas que se encuentran atras de Munay que se va a detener, evitando posibles accidentes.

Evite operar el vehículo con luces defectuosas o con la falta de alguna.
Si necesita cambiar alguna luz consulte el esquemático del cableado.
De ser posible evite cambiar o arreglar usted mismo el cableado, en su lugar recurra a un personal capacitado. Asegurese de apagar todas las luces luego de una jornada de trabajo en el vehículo.

## 7.2 Precauciones

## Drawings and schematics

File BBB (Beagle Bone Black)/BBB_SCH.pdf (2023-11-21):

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
# eMMC FLASH

9

3

2

# HDMI FRAMER

# 10/100 ETHERNET

10

# DDR3 MEMORY

# PROCESSOR 2 OF 3, UAB PORTS

7

# LED, CONFIGURATION AND BUTTON

PAGE NO. | SCHEMATIC PAGE

# PROCESSOR 3 OF 3

# PROCESSOR 1 OF 3, JTAG HEADER

4

# POWER MANAGEMENT

5

# COVER PAGE

6

# This schematic is *NOT SUPPORTED* and DOES NOT constitute a reference design. Only "community" support is allowed via

resources at BeagleBoard.org/discuss.

# THERE IS NO WARRANTY FOR THIS DESIGN, TO THE EXTENT PERMITTED BY APPLICABLE LAW. EXCEPT WHEN OTHERWISE STATED IN WRITING THE COPYRIGHT HOLDERS AND/OR OTHER PARTIES

PROVIDE THE DESIGN "AS IS" WITHOUT WARRANTY OF ANY KIND, EITHER EXPRESSED OR IMPLIED, INCLUDING, BUT NOT LIMITED TO,

# THE IMPLIED WARRANTIES OF MERCHANTABILITY AND FITNESS FOR A PARTICULAR PURPOSE. THE ENTIRE RISK AS TO THE QUALITY AND PERFORMANCE OF THE DESIGN IS WITH YOU. SHOULD THE DESIGN PROVE DEFECTIVE, YOU ASSUME THE COST OF ALL NECESSARY

SERVICING, REPAIR OR CORRECTION.

# 11 EXP CONN, uSD

REV | Description | DATE | BY
A4A | Initial production Release. | 11/19/2012 | GC
A5 | On the initial production release the processors were to be found incorrect as supplied by TI.
| Parts while marked AM3359 were actually AM3352. This revision uses the correct parts. | 1/2/2013 | GC
1. Deleted R29-R44 from the LCD lines.
2. Added 47pf capacitors C156-C173 to LCD data lines to ground.
3. Changed schematic revision to A5A.

A5A

4. Changed a few footprints after PCB update for above changes.
| 5. Added access point for the battery function of the TPS65217C. | 2/8/2013 | GC

# 7. Added power button to enable sleep, wakeup, power down and power up features on the

| system.

# 6. Added Ferrite beads in series with LED power and 5V power rail of the USB host

connector. Required to pass FCC/CE testing due to noise emissions on that pin.

A5B

# 1. Added 100K pulldown on J1 pin 4 to prevent crosstalk when serial cable is

not connected into PCB layout.
2. Changed the LED resistors to 4.75K to lower the brightness.

5/21/2013

# 8. Added Modification to add 100K ohm resistor to ground to prvent crosstalk when serial

cable is not plugged in.

GC

A5C | 6/12/2013 | GC
1. Changed R46, R47,R48 to 0 ohms.
2. Changed R45 to 22 Ohms.
Change was made due to production failures on some boards due to differences in impedances.

A6

# 1. Moved the enable for the VDD_3V3B regulator to VDD_3V3A rail. Change was made to

reduce the delay between the ramp up of the 3.3V rails.
2. Added a AND gate to the SYS_RESETn circuitry. There is a small chance that on power up | 7/25/2013 | GC

# the nRESETOUT signal on the processor may go high, causing the SYS_RESETn signal to go

HI before it should. This change reenforces the reset with the PORZn reset signal.
3. Added optional zero ohm resistor to tie GND_OSC0 to system ground.
A6A | | 12/13/2013 | GC
1. Added optional zero ohm resistor to tie GND_OSC1 to system ground.
2. Changed C106 to a 1uF capacitor.
3. Changed C24 to a 2.2uF capacitor.
B | 1. Changed the processor to the AM3358BZCZ100. | 1/20/2014 | GC
4. Made R8 installed and R9 not installed.
C | 1. Increased the eMMC from 2GB to 4GB; The PCB revision for this board is Rev B6. | 3/21/2014 | GC

C3

1. Page 3: Added series resistor (R35,R36,R43,R44,R168-R173)=33R to the MMC1 lines,
C175=DNI(10pF) to the MMC1_CLK to DGND; Changed C24 from 2.2uF to DNI.

4/1/2021

3. Page 8: Connected the Pin A6 J5 of U13(eMMC IC) to DGND.
4. Page 9: Added AM3358 GPIO1_8 and a Positive-AND gate(U1) to reset ethernet LAN8710A; Added series resistor (R38-R42)=33R to the LAN8710A TX lines;
Changed (C137-C140) from DNI to 10pF.

# 5. Page 11: Changed the MicroSD Connector from ALPS_SCHA5B0200 (EOL) to YU LIANG_YL004-030-001; Added series resistor (R2,R13,R15,R16,R31,R32)=33R

and C5=DNI(10pF) to the MMC0 lines.

# JQ.Xin

6. The PCB Revision for this board is RevC, BOM is RevC3.
2. Page 4: Changed USB1_VBUS series resistor from FB8=0.1R 0805 to R37=0R 0402.

# Title

Size Document Number | Rev
Date: | Sheet | of
450-5500-001 | C3

# BeagleBone Black Cover Page

B
Thursday, April 01, 2021 | 1 | 11

# Title

Size Document Number | Rev
Date: | Sheet | of
450-5500-001 | C3

# BeagleBone Black Cover Page

B
Thursday, April 01, 2021 | 1 | 11

# Title

Size Document Number | Rev
Date: | Sheet | of
450-5500-001 | C3

# BeagleBone Black Cover Page

B
Thursday, April 01, 2021 | 1 | 11
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

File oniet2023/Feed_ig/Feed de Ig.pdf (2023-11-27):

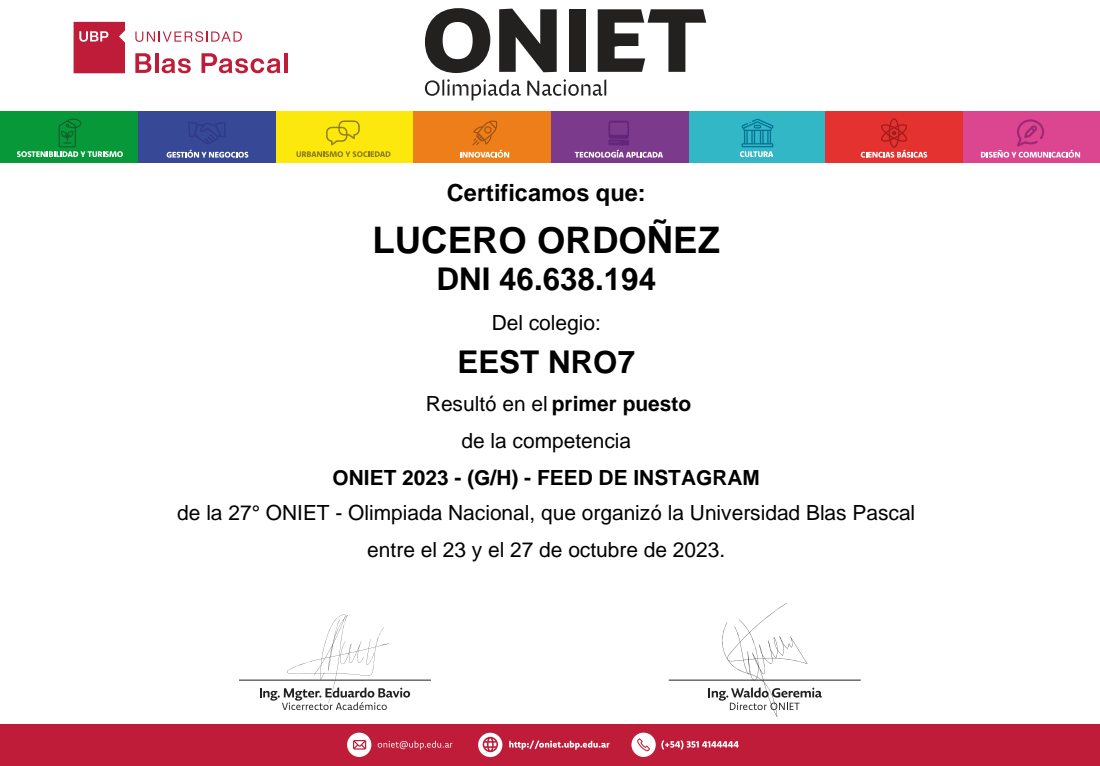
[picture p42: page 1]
Certificamos que: LUCERO ORDOÑEZ DNI 46.638.194; Del colegio: EEST NRO7

Resultó en el primer puesto
de la competencia

ONIET 2023 - (G/H) - FEED DE INSTAGRAM

de la 27° ONIET - Olimpiada Nacional, que organizó la Universidad Blas Pascal

entre el 23 y el 27 de octubre de 2023.

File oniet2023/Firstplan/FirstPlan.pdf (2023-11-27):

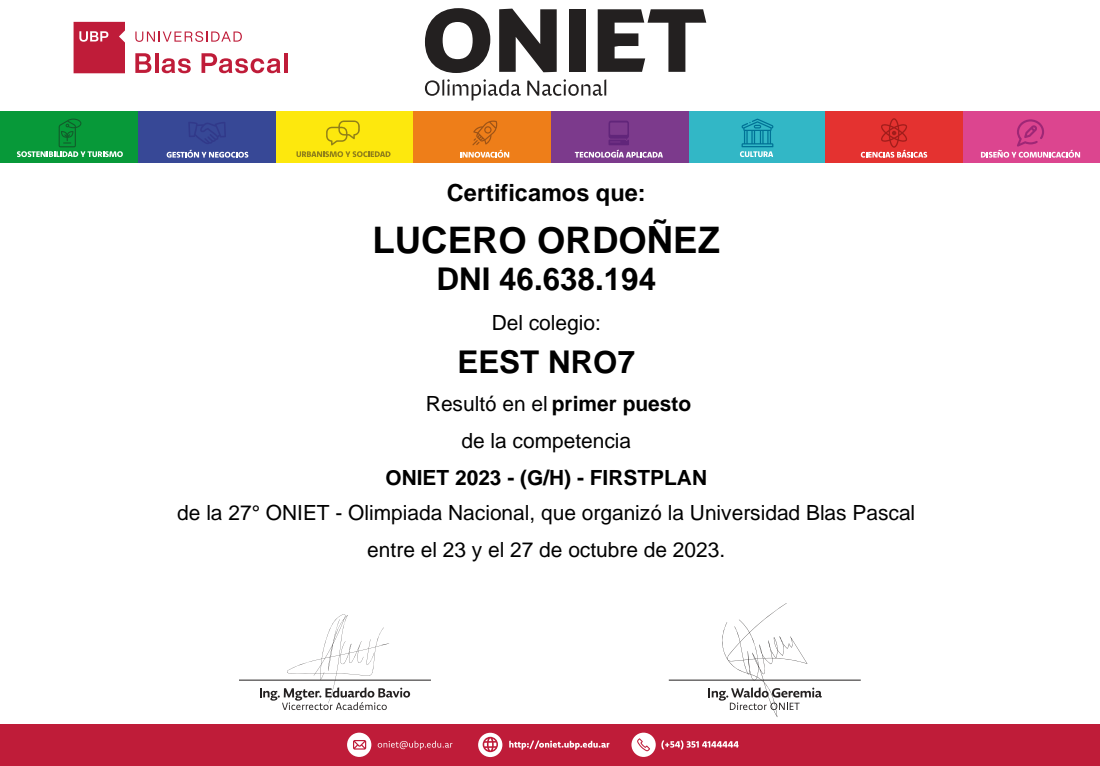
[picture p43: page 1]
Certificamos que: LUCERO ORDOÑEZ DNI 46.638.194; Del colegio: EEST NRO7; ONIET 2023 - (G/H) - FIRSTPLAN

Resultó en el primer puesto
de la competencia

de la 27° ONIET - Olimpiada Nacional, que organizó la Universidad Blas Pascal

entre el 23 y el 27 de octubre de 2023.

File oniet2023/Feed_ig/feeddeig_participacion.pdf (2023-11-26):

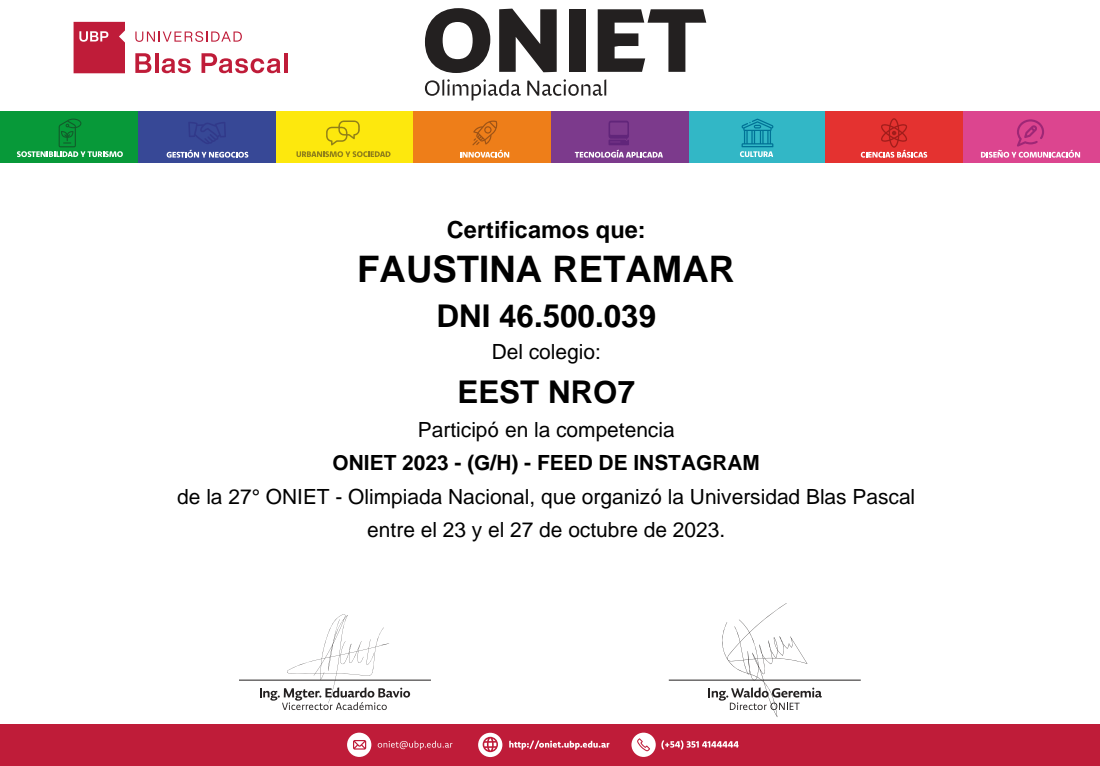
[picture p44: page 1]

Certificamos que:
FAUSTINA RETAMAR
DNI 46.500.039
Del colegio:
EEST NRO7
Participó en la competencia

ONIET 2023 - (G/H) - FEED DE INSTAGRAM

de la 27° ONIET - Olimpiada Nacional, que organizó la Universidad Blas Pascal

entre el 23 y el 27 de octubre de 2023.

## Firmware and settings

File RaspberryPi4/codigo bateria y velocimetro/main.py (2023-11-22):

from flask import Flask, render_template, jsonify
import RPi.GPIO as GPIO
import time
speed=0

app = Flask(__name__)

try:
    # Intentar importar módulos específicos que dependen del ADC
    import board
    import busio
    import adafruit_ads1x15.ads1115 as ADS
    from adafruit_ads1x15.analog_in import AnalogIn

    # Intentar crear el objeto I2C bus y ADC
    i2c = busio.I2C(board.SCL, board.SDA)
    ads = ADS.ADS1115(i2c)

    # Crear un canal de entrada analógica en el ADC
    chan = AnalogIn(ads, ADS.P0)

    # Definir la función int0 después de haber importado el módulo
    def int0(channel):
        global up_times, index, m2
        m1 = time.time()
        up_times[index] = (m1 - m2) * 1E6
        index = (index + 1) % 3
        m2 = m1
except ImportError:
    print("Error: No se pudo importar el módulo del ADC. El ADC no estará disponible.")
    chan = None  # Configurar chan como None si el ADC no está disponible
    encoder_reading_pin = None  # Configurar encoder_reading_pin como None si el ADC no está disponible
except Exception as e:
    print(f"Error initializing ADC: {e}")
    chan = None  # Configurar chan como None si la inicialización falla
    encoder_reading_pin = None  # Configurar encoder_reading_pin como None si la inicialización falla

# Configuración de GPIO si encoder_reading_pin está definido
if encoder_reading_pin is not None:
    GPIO.setmode(GPIO.BCM)

    # Variables para el medidor de velocidad
    encoder_reading_pin = 17
    up_times = [0, 0, 0]
    index = 0
    m2 = time.time()
    speed = 0

    GPIO.setup(encoder_reading_pin, GPIO.IN, pull_up_down=GPIO.PUD_UP)
    GPIO.add_event_detect(encoder_reading_pin, GPIO.BOTH, callback=int0)


# Función para calcular el porcentaje de carga de la batería
def calculate_percentage_charge(adc_voltage):
    if adc_voltage is None:
        return 0  # Default to 0% if ADC is not initialized

    # Define las variables de la batería
    voltage_divider_ratio = 15
    battery_voltage_min = 0.0 * 12  # 2.4V per cell for a 12-cell battery
    battery_voltage_max = 4.0 * 12  # 4.2V per cell for a 12-cell battery

    # Calcula el voltaje de la batería y el porcentaje de carga
    battery_voltage = adc_voltage * voltage_divider_ratio

    if battery_voltage < battery_voltage_min or battery_voltage > battery_voltage_max:
        return 0  # Default to 0% if voltage is out of range

    percentage_charge = ((battery_voltage - battery_voltage_min) / (battery_voltage_max - battery_voltage_min)) * 100

    if percentage_charge < 0:
        percentage_charge = 0
    elif percentage_charge > 100:
        percentage_charge = 100

    return percentage_charge


# Endpoint para obtener el porcentaje de batería
@app.route("/get_battery_percentage", methods=["GET"])
def get_battery_percentage():
    # Leer el voltaje del ADC
    if chan is None:
        adc_voltage = 0  # Default to 0 if ADC is not initialized
    else:
        adc_voltage = chan.voltage

    # Calcular el porcentaje de carga
    percentage_charge = calculate_percentage_charge(adc_voltage)

    # Devolver el porcentaje en formato JSON
    return jsonify({"percentage": percentage_charge})

# Endpoint para obtener la velocidad actual
@app.route("/get_motor_speed", methods=["GET"])
def get_motor_speed():
    global speed
    return jsonify({"speedd": speed})

# Renderizar la plantilla con los valores del porcentaje y la velocidad
@app.route("/")
def index():
    return render_template("index.html", percentage=0, speedd=0)

if __name__ == "__main__":
    app.run()

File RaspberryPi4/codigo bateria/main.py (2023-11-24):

from flask import Flask, jsonify, render_template
import time
import board
import busio
import adafruit_ads1x15.ads1115 as ADS
from adafruit_ads1x15.analog_in import AnalogIn
#para iniciar aplicacion flask
app = Flask(_name_)

# Create the I2C bus and ADC object
i2c = busio.I2C(board.SCL, board.SDA)
ads = ADS.ADS1115(i2c)

# Create an analog input channel on the ADC
chan = AnalogIn(ads, ADS.P0)

# Define the voltage divider ratio
voltage_divider_ratio = 15

# Define the battery capacity in Ah
battery_capacity = 100

# Define the battery voltage range
battery_voltage_min = 0.0 * 12  # 2.4V per cell for a 12-cell battery
battery_voltage_max = 4.0 * 12  # 4.2V per cell for a 12-cell battery

def calculate_percentage_charge(adc_voltage):
    # Calculate the battery voltage
    battery_voltage = adc_voltage * voltage_divider_ratio

    # Check if the battery voltage is within the expected range
    if battery_voltage < battery_voltage_min or battery_voltage > battery_voltage_max:
        return 0  # Default to 0% if voltage is out of range

    # Calculate the percentage of charge
    percentage_charge = ((battery_voltage - battery_voltage_min) / (battery_voltage_max - battery_voltage_min)) * 100

    # Check if the percentage of charge is within the expected range
    if percentage_charge < 0:
        percentage_charge = 0
    elif percentage_charge > 100:
        percentage_charge = 100

    return percentage_charge


@app.route("/")
def index():
    # Render the template with the percentage value
    return render_template("index.html", percentage=0)

if _name_ == "_main_":
    app.run()


@app.route("/get_battery_percentage")
def get_battery_percentage():
    # Read the voltage from the ADC
    adc_voltage = chan.voltage

    # Calculate the percentage of charge
    percentage_charge = calculate_percentage_charge(adc_voltage)

    # Return the percentage in JSON format
    return jsonify({"percentage": percentage_charge})

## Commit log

2023-10-18 feat: agregar raspberry pi4
2023-11-16 feat: agregar carpeta tecnica, campo y manual de usuario
2023-11-17 docs: agregar documentacion, carpeta tecnica, campo y manual de usuario
2023-11-21 feat: cargando codigo de velocimetro
2023-11-21 docs: carga de banner
2023-11-21 style: cambio de nombre de una carpeta
2023-11-21 feat: subida de carpeta con todos los logos necesitados para publicaciones
2023-11-21 style: cambio de nombre
2023-11-21 feat: subida de imagenes usadas en publicaciones
2023-11-21 style: cambio de nombre a la carpeta reuniones diarias
2023-11-21 feat: carga de fotos del auto en sus inicios
2023-11-21 docs: agregar documentacion de BeagleBonBlack
2023-11-21 feat: documentacion e imagenes de las baterias
2023-11-21 docs: subir documentacion de motores y controladores
2023-11-21 style: cambio de nombre de la reunion diaria 10
2023-11-21 style: cambio de nombre al archivo
2023-11-21 style: cambiar el nombre de los archivos
2023-11-21 style: cambio de nombre de archivo
2023-11-21 feat: agregar archivo solid works volante
    [Cubierta Volantero.SLDPRT]
2023-11-21 fix: eliminar carpeta volante
    [Cubierta Volantero.SLDPRT]
2023-11-21 feat: Archivo de SolidWorks Tablet
    [Funda Tablet Bien 3.SLDPRT]
2023-11-21 feat: Archivo STL Tablet
    [Funda Tablet Bien 3.STL]
2023-11-21 fix: Correccion de una Carpeta innecesaria
    [Funda Tablet Bien 3.SLDPRT]
2023-11-21 feat: Archivo de SolidWorks Tablet Derecha
    [Embellesedor Parte DER.SLDPRT]
2023-11-21 feat: Archivo SolidWorks Tablet Izquierda
    [Embellesedor Parte IZQ.SLDPRT]
2023-11-21 feat: Archivo STL Tablet Izquierda
    [Embellesedor Parte IZQ.STL]
2023-11-21 feat: Archivo STL Tablet Derecha
    [Embellesedor Parte DER.STL]
2023-11-21 feat: agrego Archivo SolidWorks
    [Camara Piso.SLDPRT]
2023-11-21 feat: Agrego Archivo STL
    [Camara Piso.STL]
2023-11-22 feat: diagrama de circuito votol
2023-11-22 feat: function connector
2023-11-22 feat: hall connector
2023-11-22 feat: alarm connector
2023-11-22 feat: esquematico de XL6009 step up
2023-11-22 feat: esquematico de LM2596 step down
2023-11-22 style: cambio de nombre de los archivos
2023-11-22 style: modificacion en el nombre de la carpeta
2023-11-22 style: cambio de nombre a la carpeta
2023-11-22 chore: modificaciones en el codigo main.py
2023-11-22 style: correccion nombre de pdf
2023-11-22 style: correccion en el nombre del archivo
2023-11-22 style: modificacion de nombre
2023-11-22 style: modificacion nombre de carpeta
2023-11-24 feat: agrego archivo 3D
    [Parrilla Sin Refuerzo.SLDPRT]
2023-11-24 chore: Reemplazo de Archivo Erroneo
2023-11-24 feat: Agrego esquema 3D
    [Estrructura Caja.SLDPRT]
2023-11-24 feat: Agregro Archivo SolidWorks
    [Palanca de Cambios.SLDPRT]
2023-11-24 chore: correción de tipeo en el código
2023-11-24 feat: subir presupuesto del proyecto
    [Plantilla de compras.xlsx]
2023-11-24 docs: adición de carpeta
2023-11-24 style: correccion del nombre de un archivo
2023-11-24 style: cambio de nombre a un archivo
2023-11-24 style: modificacion al nombre de una carpeta
